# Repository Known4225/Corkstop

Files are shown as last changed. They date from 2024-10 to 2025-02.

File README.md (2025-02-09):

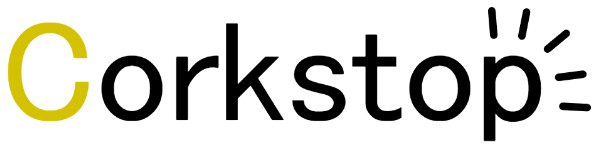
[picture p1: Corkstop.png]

### Remote Ignition System
Corkstop is a single channel ignition system that operates alongside an e-match or igniter to remotely launch a rocket or activate a stationary rocket motor.

## Power:
Corkstop uses a 14v, 24A custom battery to ignite e-matches and igniters.
## Range:
Corkstop uses a 433MHz LoRa radio, meaning it should support ranges up to half a mile or more in optimal conditions.
## How to use:
Connect the battery to the XT60 plug on the receiver box, use the alligator clips from the receiver box to connect an e-match or igniter. The continuity LED on the receiver will indicate whether the match is properly connected. GREEN indicates continuity, while RED indicates that the circuit is broken. There is no power switch on the receiver, it is active at all times if the battery is plugged in.

Continuity information is also available through the continuity LED on the controller. The controller has a power switch. The blue RF light will pulse on and off once a second, if the blue RF light is not pulsing then it means the controller could not connect to the receiver. Verify both RF connectivity and circuit continuity before attempting to ignite.

To ignite the charge, hold down the blue ARM button and verify that the control box is emitting an audible tone. Then, with the ARM button held down, press the red IGNITE button. This will light the e-match or igniter on the receiver side.

## Design Sketch:

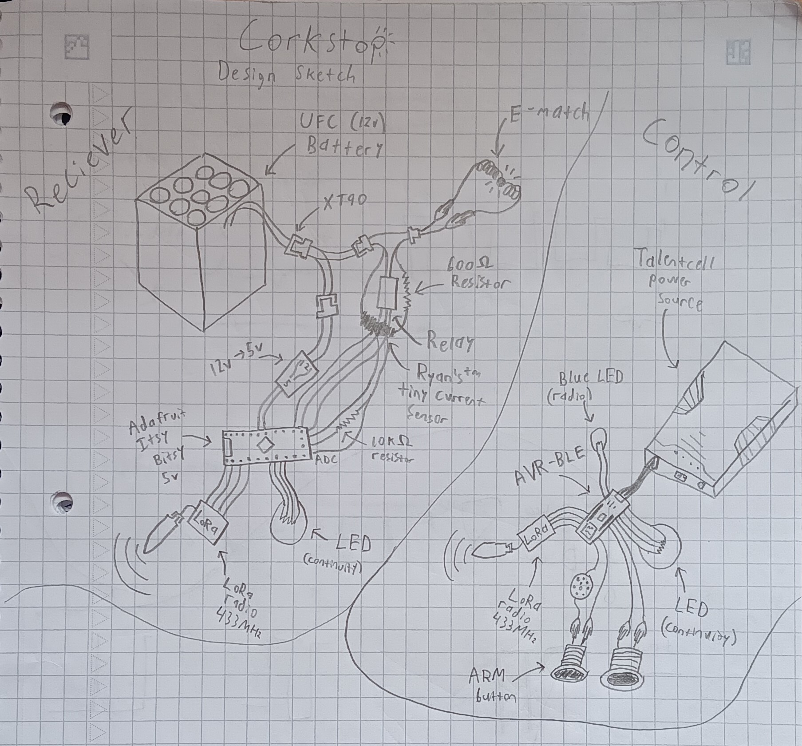
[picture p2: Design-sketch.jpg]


*note that the battery is actually 14v, not 12v. And the resistor value has been updated to 700Ω
*note that the XT60 connector is used, not the XT90

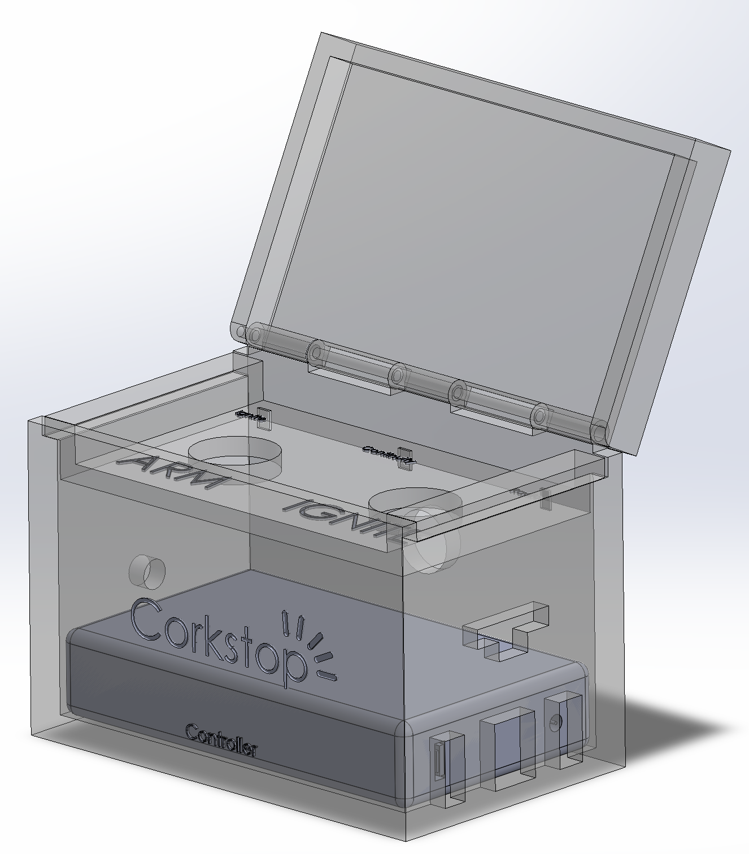
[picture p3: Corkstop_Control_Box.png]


## Product:



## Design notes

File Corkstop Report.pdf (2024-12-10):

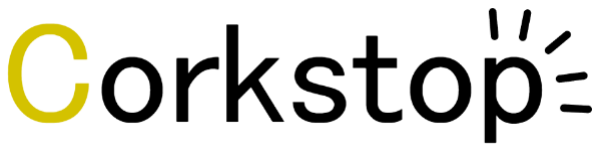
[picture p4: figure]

## Remote Ignition System

Corkstop is a single channel ignition system that operates alongside an e-match or igniter to remotely launch a rocket or activate a stationary rocket motor.

This project was made for use on the UMN rocket team (https://rkt.aem.umn.edu/) as an SRAD (student research and developed) remote ignition system for test rockets, static fires, and launches.

Corkstop consists of a controller box and receiver box, each equipped with a microcontroller, radio, and portable power source.

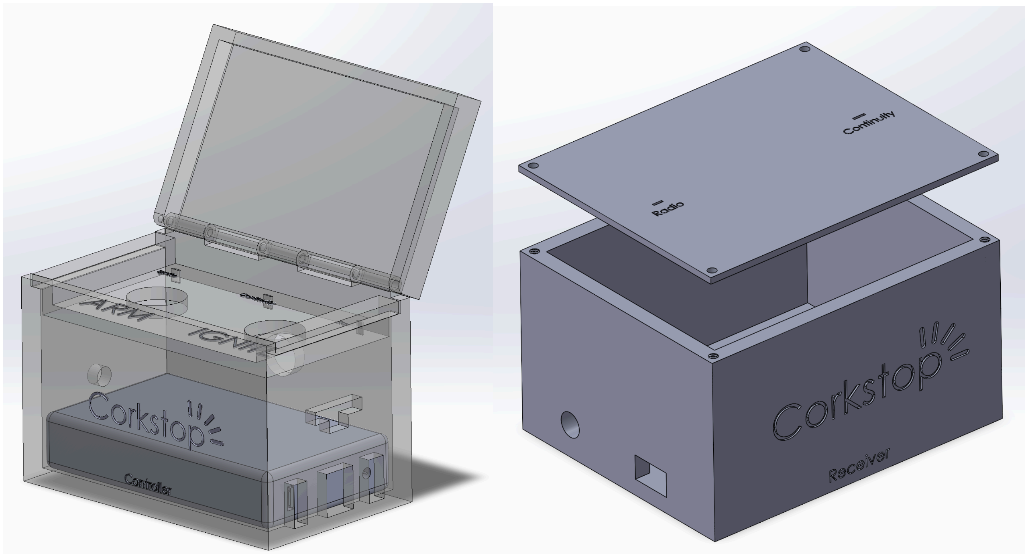
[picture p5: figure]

All the code and CAD can be found here. (https://github.com/Known4225/Corkstop)

# Design and Implementation

Here is the full BOM for this project:
1x Portable power source (https://www.amazon.com/TalentCell-Rechargeable-12000mAh-Multi-led-indicator/dp/B00ME3ZH7C)

1x AVR-BLE board (https://www.microchip.com/en-us/development-tool/dt100111)
1x ItsyBitsy 5v board (https://www.adafruit.com/product/3677)
2x LoRa breakout (https://www.adafruit.com/product/3072)
2x 433MHz antenna (https://www.amazon.com/Antenna-Frequency-Connector-SMA-Male-Receivers/dp/B0C1FCZM94)
1x XT60 Splitter (https://www.amazon.com/RIIEYOCA-Connector-Extension-Quadcopter-XT60-Male/dp/B09L62W679)
2x XT60 connector (https://www.amazon.com/Upgrade-Extension-Connector-Adapter-Silicone/dp/B0B4H5CCR3)
1x DC Buzzer (https://www.amazon.com/Electronic-Continuous-Computers-Automotive-Equipment/dp/B08KW6HB1P)
1x DC-DC converter (https://www.amazon.com/Converter-Voltage-Waterproof-Regulator-Step-Down/dp/B07Y2V1F8V)
1x 5v Relay (https://www.amazon.com/Tolako-Arduino-Indicator-Channel-Official/dp/B00VRUAHLE)
1x 700Ω resistor (https://www.digikey.com/en/products/detail/vishay-dale/CW02B700R0JE70/1169042)
2x Arcade button (https://www.amazon.com/EG-STARTS-Illuminated-Buttons-Raspberry/dp/B01N11BDX9)
2x Alligator Clips
1x Photoresistor
1x Blue LED
2x Cyan LED
3x Multicolour LED
1x 10kΩ resistor
∞x E-matches
1x UFC battery (12.7v, pictured below)

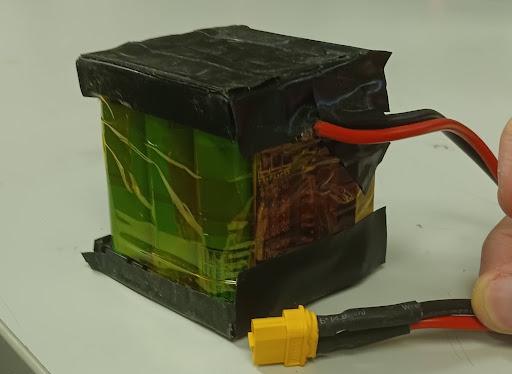
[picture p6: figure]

## Circuit:

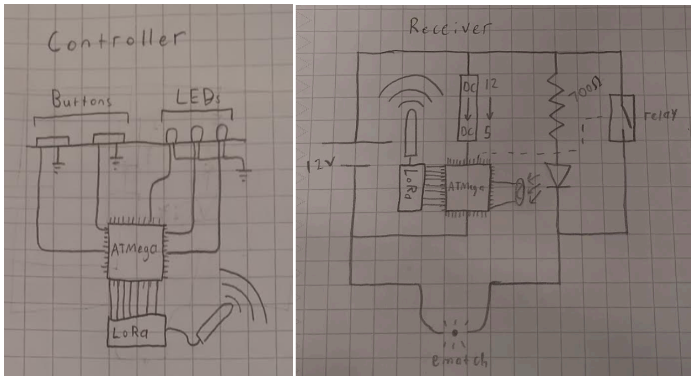
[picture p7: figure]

The basic idea is that a large amount of current (> 300mA) will cause the ematch to ignite. That current is supplied by the UFC battery on the receiver’s end. When the relay is triggered, the battery is shorted, causing a large amount of current to flow through the ematch. While the relay is not triggered, there is a small amount of current (about 15 milliamps) flowing through the ematch. This current is not enough to blow the ematch, but it is enough to light an LED (pictured directly below the 700Ω resistor). The light from the LED is detected by a photoresistor, and the information is recorded by the ATMega on the receiver.

If the ematch is connected improperly, or not connected at all, then the LED is not glowing, as the circuit is not complete. This is called continuity. When the circuit is closed it is said to “have continuity”, when it is open it “does not have continuity”. Both the receiver and controller boxes have a continuity status light, which is green to indicate continuity, and red to indicate loss of continuity. The receiver box uses the photoresistor along with its ADC to gather this continuity information. It then sends that information to the controller box over the LoRa radio.

## Radio:

Both boxes use an SX1276 (https://cdn-shop.adafruit.com/product-files/3179/sx1276_77_78_79.pdf) LoRa radio module. These radios interface over SPI and make use of an interrupt pin for incoming messages. The Corkstop™ custom radio protocol works via request response. The controller box, if on, periodically sends the ASCII string “cork” once a second. The receiver box responds to this by sending either “stop” or “stal”. “stop” indicates that it has continuity on the circuit, and “stal” indicates no continuity. When either radio receives a message, it will turn their cyan radio LED on with a timer to expire the LED in half a second. This means that the cyan radio LED should be blinking every half second if both radios are connected. If either radio disconnects both radio lights remain off.

When the controller wants to send the ignition message, it sends the ASCII string “IGNITE”. The receiver will, after verifying continuity, trigger the relay to short the circuit. If continuity is not met when the ignition signal is received, the receiver will not trigger the relay and will send back “cant” in response. Otherwise, the relay will be triggered for 0.1 seconds and the receiver will send back “done” in response. The closing of the relay should ignite the ematch.

No CRC or checksums are used in the Corkstop™ custom radio protocol. Any malicious actor could send the ASCII strings over 433MHz frequency to attempt to trigger ignition. This also means that multiple Corkstop™ controller -> receiver pairs are not currently possible.

Additionally, libraries RadioHead (https://github.com/PaulStoffregen/RadioHead) and AVR_LoRa (https://github.com/kpierzynski/AVR_LoRa) were used in this project. Thanks to Paul Stoffregen, (http://paulstoffregen) Kurt E, (https://github.com/KurtE) and kpierzynski. (https://github.com/kpierzynski)

## Challenges:

This device is relatively simple, the main challenge was limited time. The initial design concept was created a month before the final product was complete, which is impressive if not a little irresponsible for a device that has a number of safety considerations.

The only design difficulty was figuring out how to integrate the continuity sensor. Current sensors exist, but most of them are not built for these small amounts of currents (10s of milliamps). The LED taped to a photoresistor is certainly unique, but non-standard and potentially dangerous. If the LED burns out then the device will report no continuity even when there is (which is the most dangerous case). I tested the merits of the idea with an arduino and a breadboard three weeks before the project was due, and it seemed like it worked (in ideal environmental conditions that is). Certainly some more thought should have been put into it.

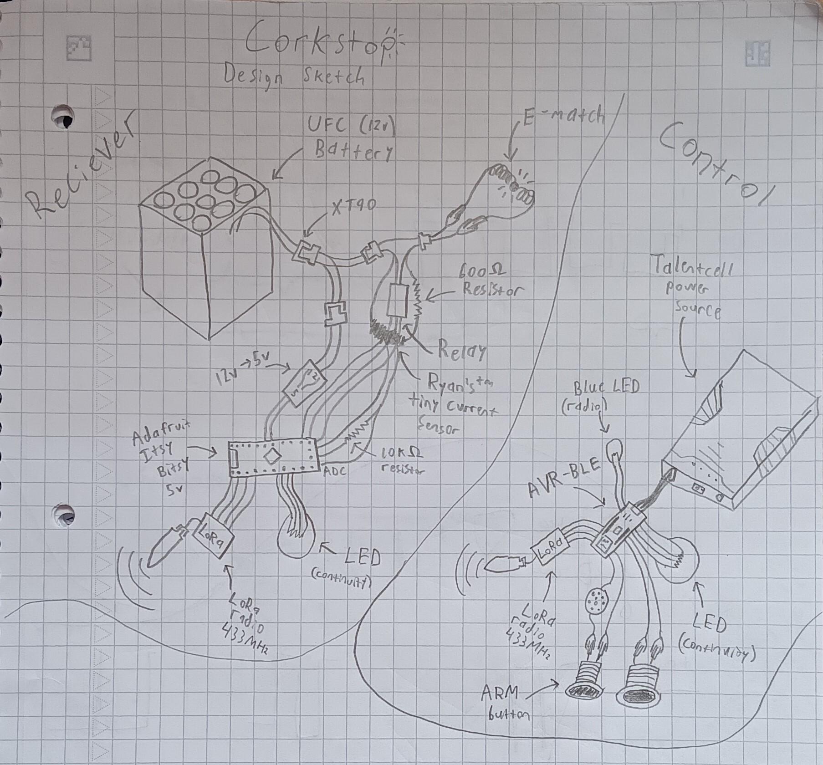
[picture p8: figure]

There were considerable manufacturing challenges, mostly due to a fairly large number of custom parts. I soldered XT60 connectors to the DC -> DC converter, as well as the resistor, current sensing LED, and alligator clips (with the heads cut off). The relay required custom wire with a molex crimp head, and that wire also had to be soldered in with the rest. I put some sleeves over the wire and heat shrunk them together, but this process was fairly difficult, especially at a three-way junction of relay, alligator clip, and LED which I had to redo twice (once when I put the LED on backwards, and again when the LED burned out under mysterious circumstances). I also needed more pins than the AVR-BLE could provide, so I ended up hijacking a few of the BLE pins (UART tx to BLE, as well as reset pin) by soldering wires onto the pads directly. That process was harder than I anticipated (and I totally destroyed the BLE in the process).

The other manufacturing challenge was CAD and 3D printing. Initial designs were finished in CAD about a week before the project was due, and I spent most of thanksgiving break printing them. Only one failed print, but some overlooked design quirks (buzzer hole was not big enough, screw taps did not work, caliper revealed that many of my holes were too small, luckily was caught before printing).

Finally, the assembly process was not difficult but was frustrating. I ended up stuffing all the wires in the box and hoping none of them disconnected. I also decided later to solder an extra antenna to the radio modules to increase range. This was very difficult to do after assembly had been completed.

# Final Product

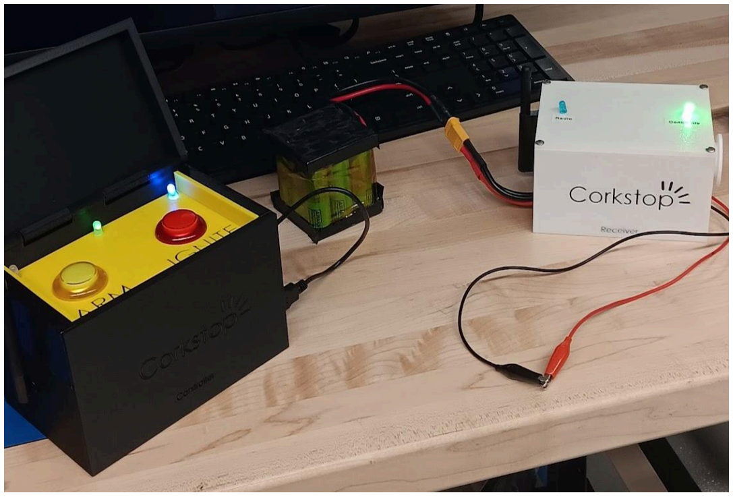
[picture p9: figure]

In total, despite the rushed process, the device was working with all of its features on demo day. There were two tests prior to the due date, one with the electronics pre-assembly and another after the project had been initially completed. Both tests successfully ignited the ematch and every feature worked. Two more ematches were ignited on demo day. The current product has a 100% success rate so far.

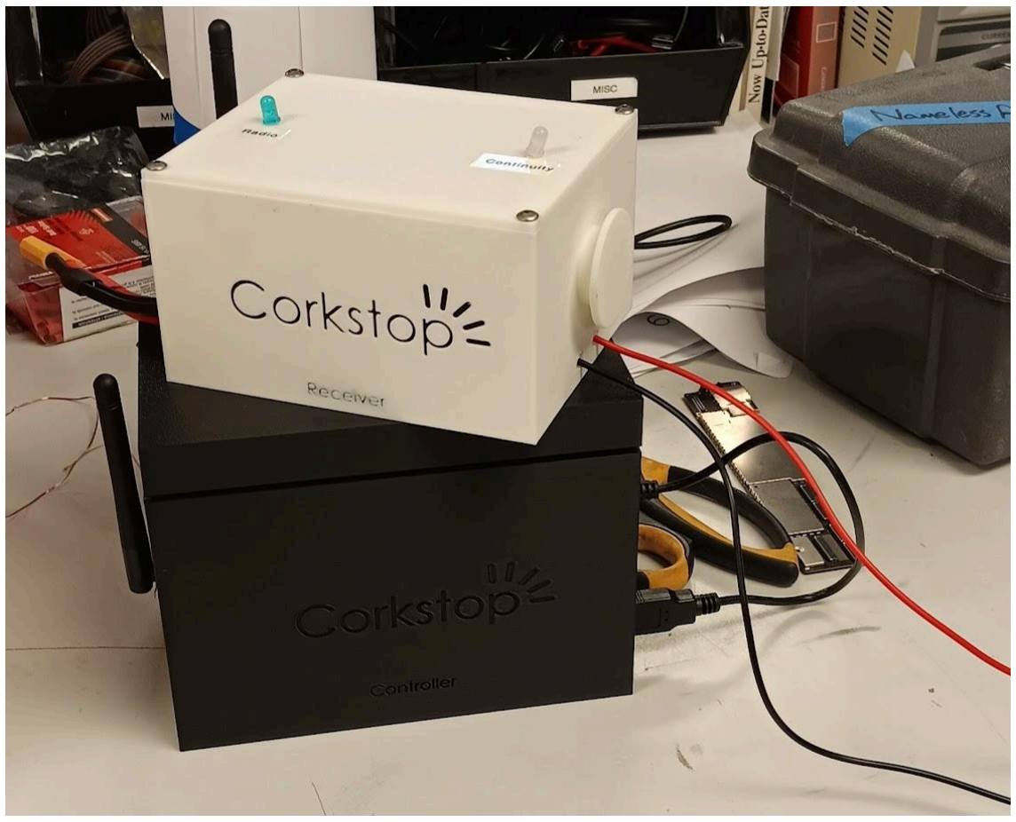
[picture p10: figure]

Every initial project goal was hit except for the range. The last range test gave poor results (~100ft), but I have added an extra antenna since then.

Overall, I am not totally satisfied by the quality and fragility of the project. I would’ve preferred it to be a lot more robust, and with more consideration for safety.

# Reflection

There are two main improvements that I would like to make to this device.

The first is radio and range. Upon testing the range of the device, it was only able to operate at around 100ft, which is not as far as the LoRa modules should be capable of. With more time and more knowledge of RF and antennas this could be improved.

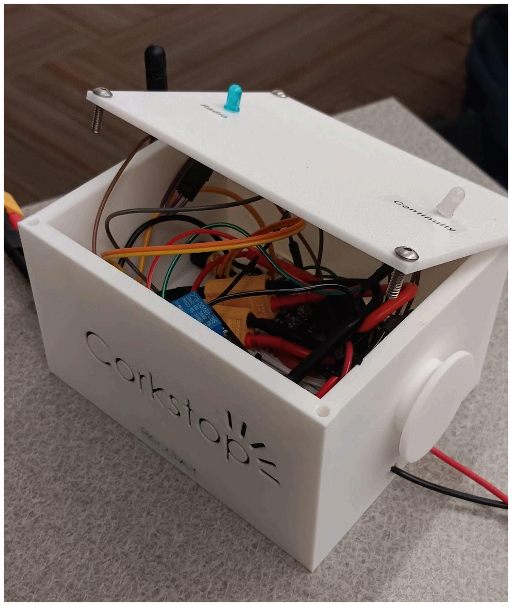
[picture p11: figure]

The second is internal wiring. It is a mess inside the boxes and it is very likely that a wire can come unplugged just by shaking the devices minimally. Ideally a whole PCB could be designed, but a solder-in breadboard would also probably suffice, along with better cable management. These boxes also probably would not fair well in unideal weather conditions. The tape on the LEDs would fail in the New Mexico Deserts, none of the boxes are waterproof, and the radios need direct line of sight.

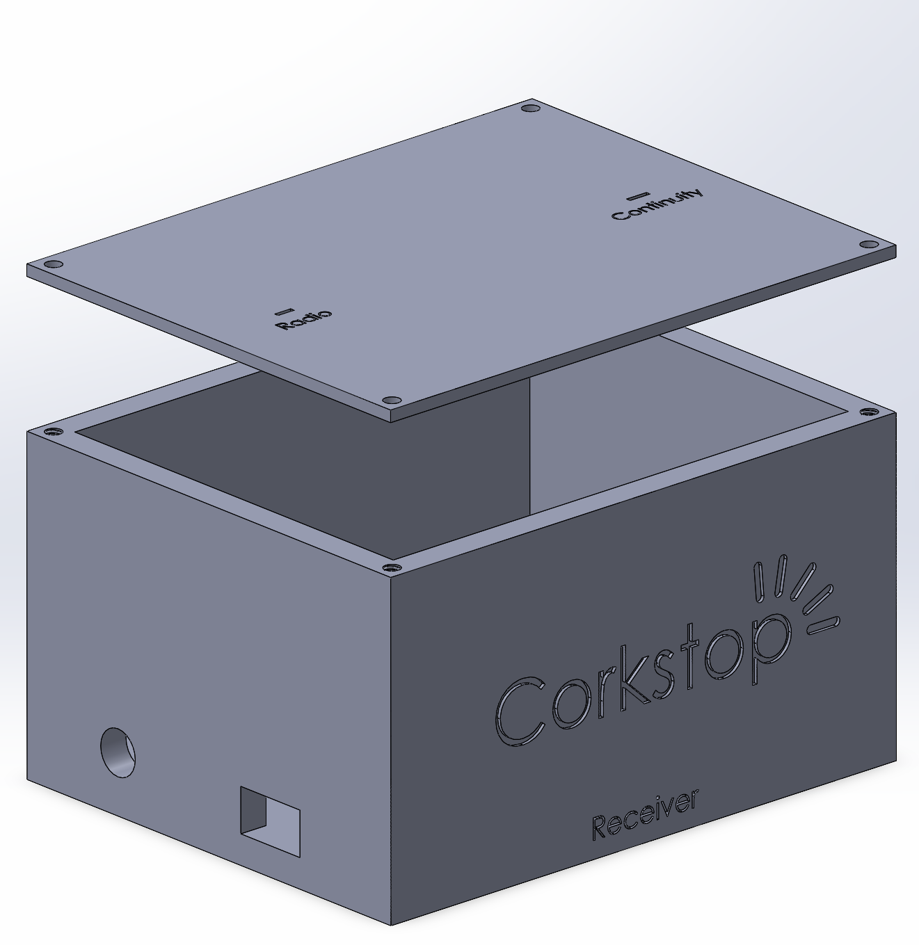
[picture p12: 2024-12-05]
Corkstop_Receive_Box.png

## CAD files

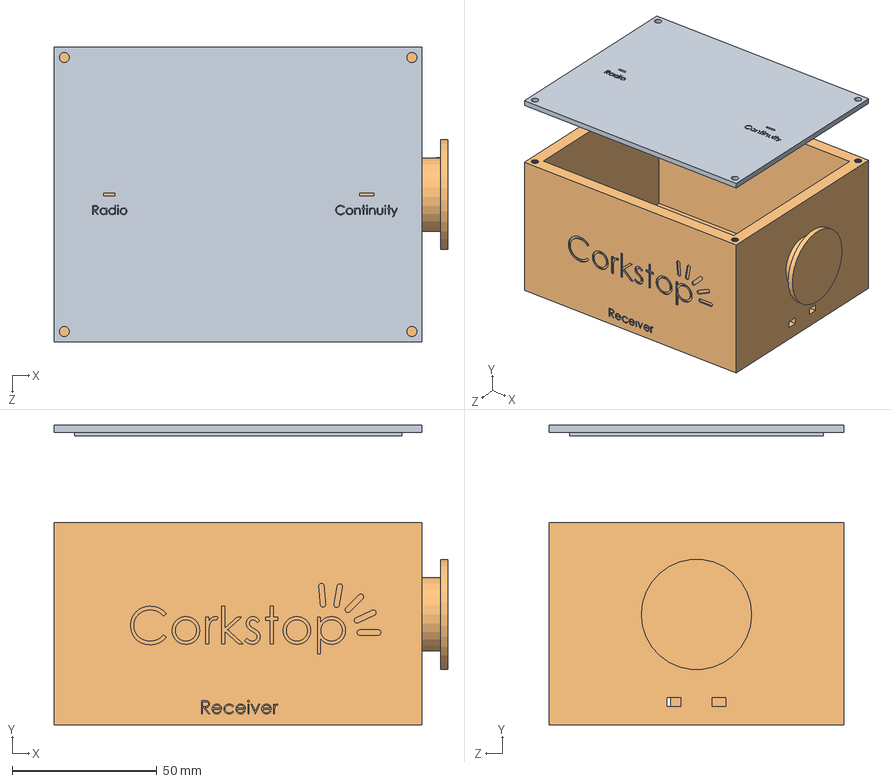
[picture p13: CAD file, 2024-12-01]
Receive.SLDASM
135.9 x 103.4 x 101.6 mm
ReceiveCase
RecieveLid

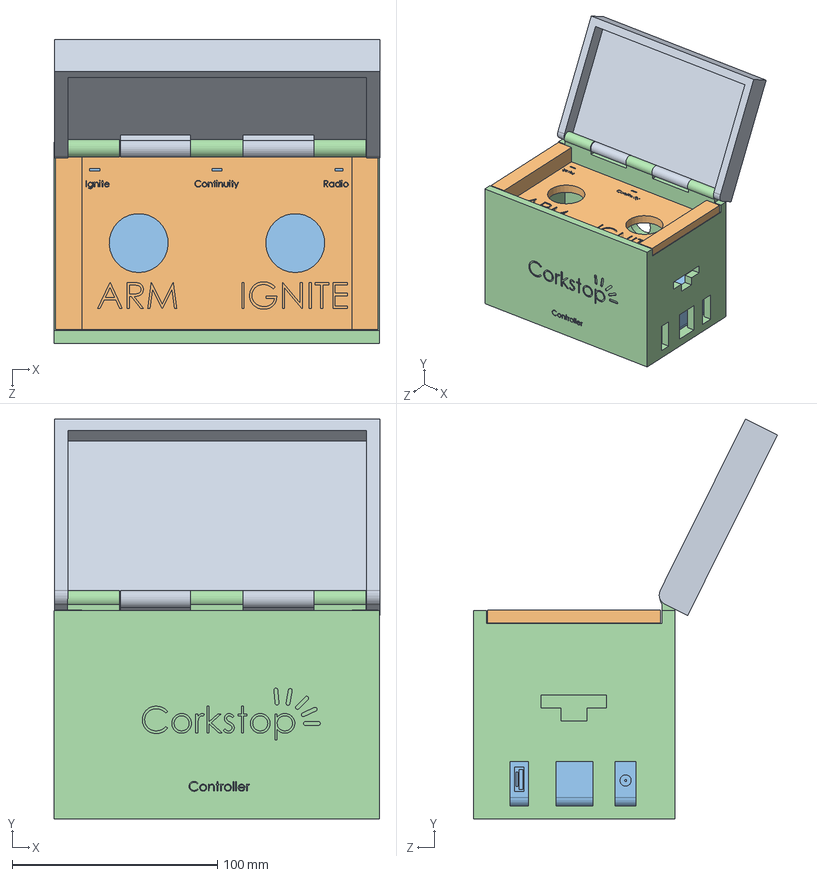
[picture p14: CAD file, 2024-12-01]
Control.SLDASM
158.5 x 194.7 x 148.0 mm
ControlCase
TalentcellPower
ControlTopShelf
ControlLid

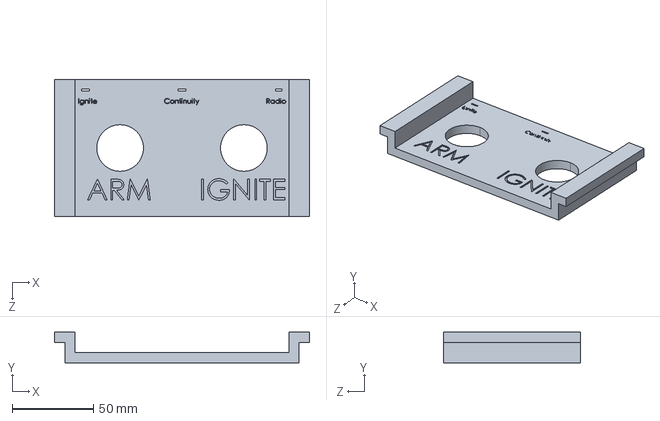
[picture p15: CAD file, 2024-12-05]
ControlBox/ControlTopShelf.STEP
157.0 x 19.0 x 84.1 mm

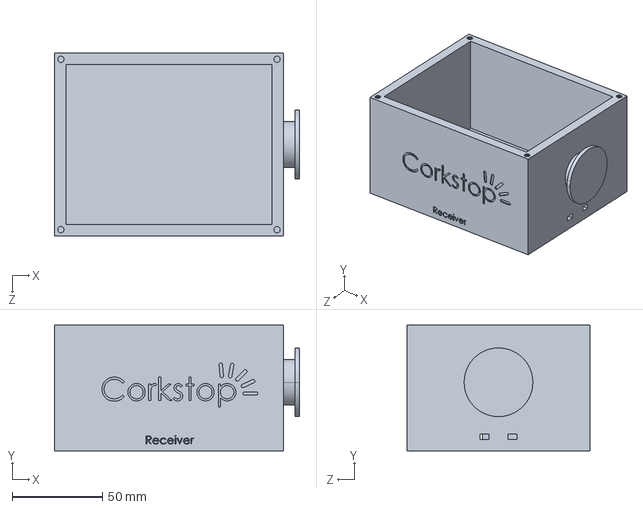
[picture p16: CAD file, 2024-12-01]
ReceiveBox/ReceiveCase.STEP
135.9 x 69.8 x 101.6 mm

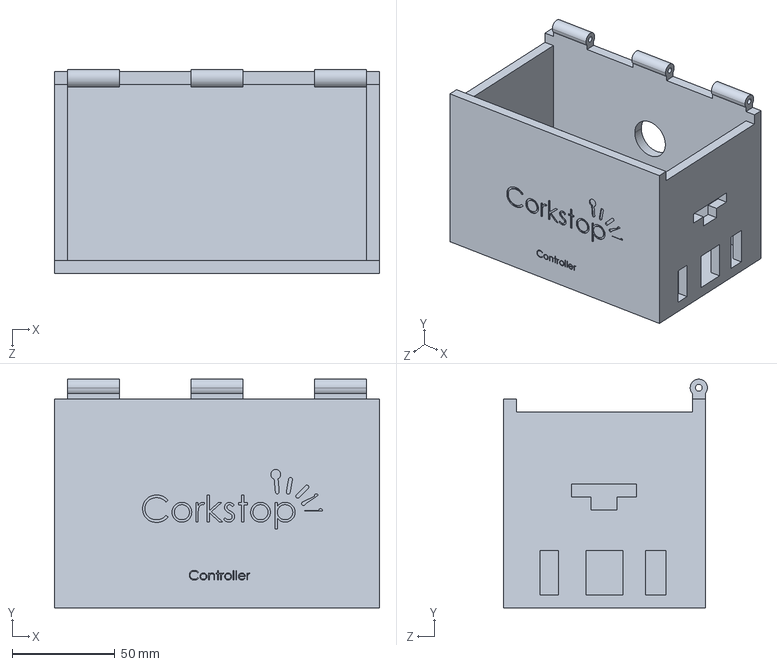
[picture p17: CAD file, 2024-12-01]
ControlBox/ControlCase.STEP
158.2 x 111.3 x 99.2 mm

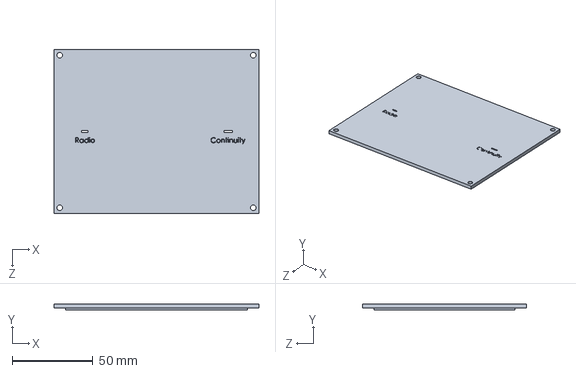
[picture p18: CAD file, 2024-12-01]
ReceiveBox/RecieveLid.STEP
127.0 x 3.81 x 101.6 mm

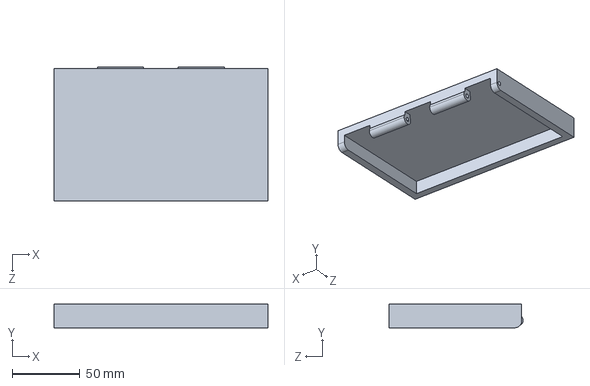
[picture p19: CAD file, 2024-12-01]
ControlBox/ControlLid.STEP
158.2 x 17.4 x 99.2 mm

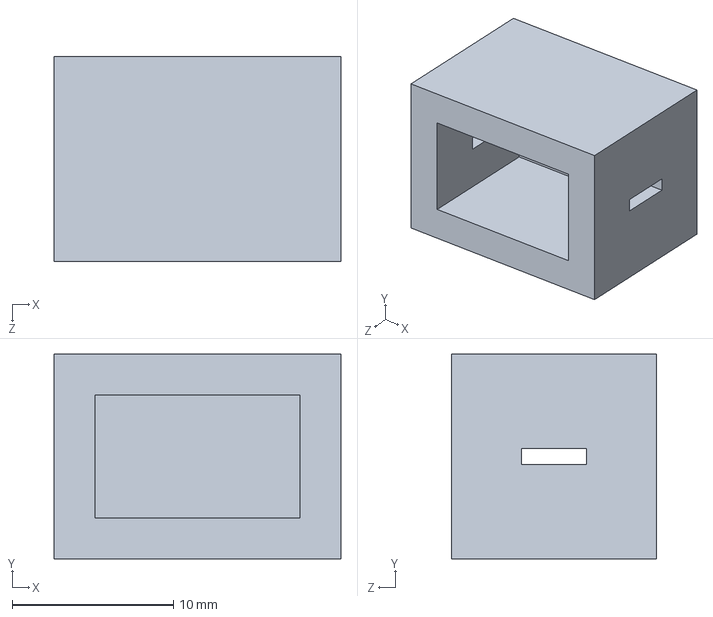
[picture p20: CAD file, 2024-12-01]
CurrentSensor.SLDPRT
17.8 x 12.7 x 12.7 mm

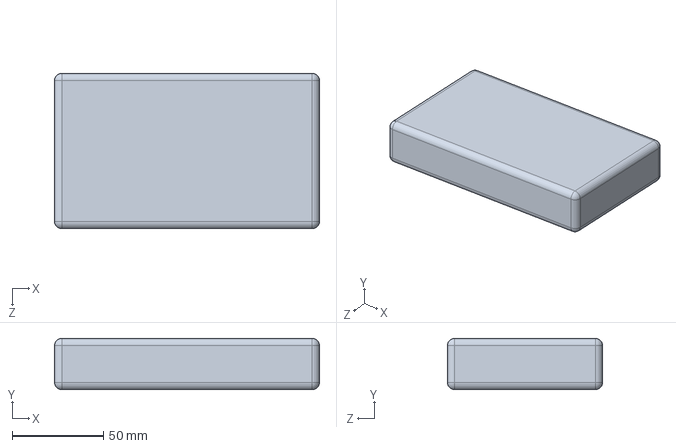
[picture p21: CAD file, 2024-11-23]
TalentcellPower.SLDPRT
145.0 x 28.0 x 85.0 mm

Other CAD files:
ControlTopShelf.SLDPRT
RecieveLid.SLDPRT
ReceiveBox/CurrentSensor.STEP
ControlLid.SLDPRT
ControlCase.SLDPRT
ReceiveCase.SLDPRT

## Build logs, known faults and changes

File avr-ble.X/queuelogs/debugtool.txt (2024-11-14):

3430 1731542538655 GEN4_TO_CONTROLLER_LOG:GEN4_CONNECT_INT_LOG Post:SetLEDBrightness
3430 1731542538655 GEN4_TO_CONTROLLER_LOG:GEN4_CONNECT_INT_LOG Return Value
3430 1731542538655 GEN4_TO_CONTROLLER_LOG:GEN4_CONNECT_INT_LOG none
3430 1731542538655 GEN4_TO_CONTROLLER_LOG:GEN4_CONNECT_INT_LOG Return End

3430 1731542538655 GEN4_TO_CONTROLLER_LOG:GEN4_CONNECT_INT_LOG Pre:SetToolInfo
3430 1731542538655 GEN4_TO_CONTROLLER_LOG:GEN4_CONNECT_INT_LOG Payload
3430 1731542538655 GEN4_TO_CONTROLLER_LOG:GEN4_CONNECT_INT_LOG ToolInfo: Values:
3430 1731542538655 GEN4_TO_CONTROLLER_LOG:GEN4_CONNECT_INT_LOG ToolInfo: speedLevel = 1, PGCResistance = 4700, PGDResistance = 4700, PGCPullDir = PullDown, PGDPullDir = PullDown, ICSPSelected = Wire2
3430 1731542538655 GEN4_TO_CONTROLLER_LOG:GEN4_CONNECT_INT_LOG Payload End
3430 1731542538655 GEN4_TO_CONTROLLER_LOG:GEN4_CONNECT_INT_LOG Post:SetToolInfo
3430 1731542538655 GEN4_TO_CONTROLLER_LOG:GEN4_CONNECT_INT_LOG Return Value
3430 1731542538655 GEN4_TO_CONTROLLER_LOG:GEN4_CONNECT_INT_LOG none
3430 1731542538655 GEN4_TO_CONTROLLER_LOG:GEN4_CONNECT_INT_LOG Return End

3430 1731542538656 GEN4_TO_CONTROLLER_LOG:GEN4_CONNECT_INT_LOG Pre:GetTargetIDInfo
3430 1731542538656 GEN4_TO_CONTROLLER_LOG:GEN4_CONNECT_INT_LOG Payload
3430 1731542538656 GEN4_TO_CONTROLLER_LOG:GEN4_CONNECT_INT_LOG null
3430 1731542538656 GEN4_TO_CONTROLLER_LOG:GEN4_CONNECT_INT_LOG Payload End
3430 1731542538656 NativeController::GetTargetIDInfo entry
3430 1731542538656 pro JtagIce3 [0x12] <<< 01 00 01 31 02 F4 01 
3430 1731542538660 pro JtagIce3 [0x12] >>> 80 00 
3430 1731542538660 pro JtagIce3 [0x12] <<< 01 00 00 00 01 05 
3430 1731542538664 pro JtagIce3 [0x12] >>> 80 00 
3430 1731542538664 pro JtagIce3 [0x12] <<< 01 00 00 01 01 01 
3430 1731542538668 pro JtagIce3 [0x12] >>> 80 00 
3430 1731542538668 pro JtagIce3 [0x12] <<< 01 00 01 00 01 08 
3430 1731542538672 pro JtagIce3 [0x12] >>> 80 00 
3430 1731542538672 pro JtagIce3 [0x12] <<< 01 00 02 00 30 00 40 80 40 00 10 80 0F 94 11 8C 0A 98 08 DC 05 DC 05 00 80 00 00 00 01 40 00 0A 05 FF 00 FF 00 00 14 00 13 00 11 80 12 8A 12 30 95 00 00 00 01 
3430 1731542538676 pro JtagIce3 [0x12] >>> 80 00 
3430 1731542538676 pro JtagIce3 [0x12] <<< 01 00 03 06 01 00 
3430 1731542538680 pro JtagIce3 [0x12] >>> 80 00 
3430 1731542538680 pro JtagIce3 [0x12] <<< 10 00 00 
3430 1731542538701 pro JtagIce3 [0x12] >>> 84 00 6D 65 67 61 00 
3430 1731542538701 pro JtagIce3 [0x12] <<< 01 00 03 06 01 00 
3430 1731542538705 pro JtagIce3 [0x12] >>> 80 00 
3430 1731542538705 pro JtagIce3 [0x12] <<< 15 00 
3430 1731542538772 pro JtagIce3 [0x12] >>> 80 00 
3430 1731542538772 pro JtagIce3 [0x12] <<< 21 00 B4 00 11 00 00 03 00 00 00 
3430 1731542538776 pro JtagIce3 [0x12] >>> 84 00 1E 95 30 00 
3430 1731542538776 pro JtagIce3 [0x12] <<< 21 00 B4 00 11 00 00 03 00 00 00 
3430 1731542538780 pro JtagIce3 [0x12] >>> 84 00 1E 95 30 00 
3430 1731542538780 pro JtagIce3 [0x12] <<< 21 00 B4 00 11 00 00 03 00 00 00 
3430 1731542538784 pro JtagIce3 [0x12] >>> 84 00 1E 95 30 00 
3430 1731542538784 pro JtagIce3 [0x12] <<< 21 00 B2 01 0F 00 00 01 00 00 00 
3430 1731542538788 pro JtagIce3 [0x12] >>> 84 00 01 00 
3430 1731542538788 pro JtagIce3 [0x12] <<< 16 00 
3430 1731542538792 pro JtagIce3 [0x12] >>> 80 00 
3430 1731542538792 pro JtagIce3 [0x12] <<< 11 00 
3430 1731542538796 pro JtagIce3 [0x12] >>> 80 00 
3430 1731542538796 pro JtagIce3 [0x01] <<< 11 00 00 
3430 1731542538800 pro JtagIce3 [0x01] >>> 80 00 
3430 1731542538800 NativeController::GetTargetIDInfo exit device ID 0x1e9530
3430 1731542538800 GEN4_TO_CONTROLLER_LOG:GEN4_CONNECT_INT_LOG Post:GetTargetIDInfo
3430 1731542538800 GEN4_TO_CONTROLLER_LOG:GEN4_CONNECT_INT_LOG Return Value
3430 1731542538800 GEN4_TO_CONTROLLER_LOG:GEN4_CONNECT_INT_LOG TargetIDInfo: Values:
3430 1731542538800 GEN4_TO_CONTROLLER_LOG:GEN4_CONNECT_INT_LOG TargetIDInfo: DeviceID = 001e9530
3430 1731542538800 GEN4_TO_CONTROLLER_LOG:GEN4_CONNECT_INT_LOG Return End

3430 1731542538804 GEN4_TO_CONTROLLER_LOG:GEN4_PROGRAM_INT_LOG_ATmega3208 Pre:SendOperation
3430 1731542538804 GEN4_TO_CONTROLLER_LOG:GEN4_PROGRAM_INT_LOG_ATmega3208 Payload
3430 1731542538804 GEN4_TO_CONTROLLER_LOG:GEN4_PROGRAM_INT_LOG_ATmega3208 OperationInfo: Values:
3430 1731542538804 GEN4_TO_CONTROLLER_LOG:GEN4_PROGRAM_INT_LOG_ATmega3208 OperationInfo: Type = erase, Mask = 00000000, Erase = false, Production Mode = true
3430 1731542538804 GEN4_TO_CONTROLLER_LOG:GEN4_PROGRAM_INT_LOG_ATmega3208 TransferInfo: Start = 0, End = 7fff, Buffer Length = 0, Type = Pgm, Mask = 00000000
3430 1731542538804 GEN4_TO_CONTROLLER_LOG:GEN4_PROGRAM_INT_LOG_ATmega3208 TransferInfo: Start = 1280, End = 1288, Buffer Length = 0, Type = Cfg, Mask = 00000000
3430 1731542538804 GEN4_TO_CONTROLLER_LOG:GEN4_PROGRAM_INT_LOG_ATmega3208 TransferInfo: Start = 128a, End = 128a, Buffer Length = 0, Type = Cfg, Mask = 00000000
3430 1731542538804 GEN4_TO_CONTROLLER_LOG:GEN4_PROGRAM_INT_LOG_ATmega3208 TransferInfo: Start = 1400, End = 14ff, Buffer Length = 0, Type = EEData, Mask = 00000000
3430 1731542538804 GEN4_TO_CONTROLLER_LOG:GEN4_PROGRAM_INT_LOG_ATmega3208 TransferInfo: Start = 1300, End = 133f, Buffer Length = 0, Type = UserID, Mask = 00000000
3430 1731542538804 GEN4_TO_CONTROLLER_LOG:GEN4_PROGRAM_INT_LOG_ATmega3208 Payload End
3430 1731542538804 pro JtagIce3 [0x12] <<< 01 00 01 31 02 F4 01 
3430 1731542538807 pro JtagIce3 [0x12] >>> 80 00 
3430 1731542538807 pro JtagIce3 [0x12] <<< 01 00 00 00 01 05 
3430 1731542538811 pro JtagIce3 [0x12] >>> 80 00 
3430 1731542538811 pro JtagIce3 [0x12] <<< 01 00 00 01 01 01 
3430 1731542538815 pro JtagIce3 [0x12] >>> 80 00 
3430 1731542538815 pro JtagIce3 [0x12] <<< 01 00 01 00 01 08 
3430 1731542538819 pro JtagIce3 [0x12] >>> 80 00 
3430 1731542538819 pro JtagIce3 [0x12] <<< 01 00 02 00 30 00 40 80 40 00 10 80 0F 94 11 8C 0A 98 08 DC 05 DC 05 00 80 00 00 00 01 40 00 0A 05 FF 00 FF 00 00 14 00 13 00 11 80 12 8A 12 30 95 00 00 00 01 
3430 1731542538823 pro JtagIce3 [0x12] >>> 80 00 
3430 1731542538823 pro JtagIce3 [0x12] <<< 01 00 03 06 01 00 
3430 1731542538827 pro JtagIce3 [0x12] >>> 80 00 
3430 1731542538827 pro JtagIce3 [0x12] <<< 10 00 00 
3430 1731542538848 pro JtagIce3 [0x12] >>> 84 00 6D 65 67 61 00 
3430 1731542538848 pro JtagIce3 [0x12] <<< 01 00 03 06 01 00 
3430 1731542538852 pro JtagIce3 [0x12] >>> 80 00 
3430 1731542538852 pro JtagIce3 [0x12] <<< 15 00 
3430 1731542538919 pro JtagIce3 [0x12] >>> 80 00 
3430 1731542538919 pro JtagIce3 [0x12] <<< 21 00 B4 00 11 00 00 03 00 00 00 
3430 1731542538923 pro JtagIce3 [0x12] >>> 84 00 1E 95 30 00 
3430 1731542538923 pro JtagIce3 [0x12] <<< 20 00 00 00 00 00 00 
3430 1731542538930 pro JtagIce3 [0x12] >>> 80 00 
3430 1731542538930 pro JtagIce3 [0x12] <<< 21 00 B2 85 12 00 00 01 00 00 00 
3430 1731542538934 pro JtagIce3 [0x12] >>> 84 00 C0 00 
3430 1731542538934 pro JtagIce3 [0x12] <<< 23 00 B2 85 12 00 00 01 00 00 00 00 C0 
3430 1731542538942 pro JtagIce3 [0x12] >>> 80 00 
3430 1731542538942 pro JtagIce3 [0x12] <<< 21 00 B2 85 12 00 00 01 00 00 00 
3430 1731542538946 pro JtagIce3 [0x12] >>> 84 00 C0 00 
3430 1731542538946 pro JtagIce3 [0x12] <<< 23 00 B2 85 12 00 00 01 00 00 00 00 C0 
3430 1731542538954 pro JtagIce3 [0x12] >>> 80 00 
3430 1731542538954 pro JtagIce3 [0x12] <<< 20 00 00 00 00 00 00 
3430 1731542538961 pro JtagIce3 [0x12] >>> 80 00 
3430 1731542538961 GEN4_TO_CONTROLLER_LOG:GEN4_PROGRAM_INT_LOG_ATmega3208 Post:SendOperation
3430 1731542538961 GEN4_TO_CONTROLLER_LOG:GEN4_PROGRAM_INT_LOG_ATmega3208 Return Value
3430 1731542538961 GEN4_TO_CONTROLLER_LOG:GEN4_PROGRAM_INT_LOG_ATmega3208 None
3430 1731542538961 GEN4_TO_CONTROLLER_LOG:GEN4_PROGRAM_INT_LOG_ATmega3208 Return End

3430 1731542538962 GEN4_TO_CONTROLLER_LOG:GEN4_PROGRAM_INT_LOG_ATmega3208 Pre:SendOperation
3430 1731542538962 GEN4_TO_CONTROLLER_LOG:GEN4_PROGRAM_INT_LOG_ATmega3208 Payload
3430 1731542538962 GEN4_TO_CONTROLLER_LOG:GEN4_PROGRAM_INT_LOG_ATmega3208 OperationInfo: Values:
3430 1731542538962 GEN4_TO_CONTROLLER_LOG:GEN4_PROGRAM_INT_LOG_ATmega3208 OperationInfo: Type = write, Mask = 00000000, Erase = false, Production Mode = true
3430 1731542538962 GEN4_TO_CONTROLLER_LOG:GEN4_PROGRAM_INT_LOG_ATmega3208 TransferInfo: Start = 0, End = cff, Buffer Length = 3328, Type = Pgm, Mask = 00000000
3430 1731542538962 GEN4_TO_CONTROLLER_LOG:GEN4_PROGRAM_INT_LOG_ATmega3208 Payload End
3430 1731542538962 pro JtagIce3 [0x12] <<< 23 00 C0 00 00 00 00 80 00 00 00 00 0C 94 4B 00 0C 94 5E 06 0C 94 5E 06 0C 94 5E 06 0C 94 5E 06 0C 94 5E 06 0C 94 E2 05 0C 94 5E 06 0C 94 5E 06 0C 94 5E 06 0C 94 5E 06 0C 94 5E 06 0C 94 5E 06 0C 94 5E 06 0C 94 5E 06 0C 94 5E 06 0C 94 5E 06 0C 94 5E 06 0C 94 5E 06 0C 94 5E 06 0C 94 5E 06 0C 94 5E 06 0C 94 5E 06 0C 94 5E 06 0C 94 5E 06 0C 94 5E 06 0C 94 5E 06 0C 94 5E 06 0C 94 5E 06 0C 94 5E 06 0C 94 5E 06 0C 94 5E 06 
3430 1731542538980 pro JtagIce3 [0x12] >>> 80 00 
3430 1731542538980 pro JtagIce3 [0x12] <<< 23 00 C0 80 00 00 00 80 00 00 00 00 0C 94 5E 06 0C 94 5E 06 0C 94 5E 06 0C 94 5E 06 30 00 31 02 80 00 11 24 1F BE CF EF CD BF DF E3 DE BF E0 E9 F0 E0 40 E0 17 C0 B5 91 A5 91 35 91 25 91 05 91 07 FD 0C C0 95 91 85 91 EF 01 F9 2F E8 2F 05 90 0D 92 A2 17 B3 07 D9 F7 FE 01 04 C0 1D 92 A2 17 B3 07 E1 F7 E5 39 F4 07 31 F7 0E 94 A5 04 0C 94 EF 05 F8 94 FF CF CF 93 DF 93 00 D0 CD B7 DE B7 0E 94 23 05 E0 E0 F4 E0 81 81 84 60 
3430 1731542538998 pro JtagIce3 [0x12] >>> 80 00 
3430 1731542538998 pro JtagIce3 [0x12] <<< 23 00 C0 00 01 00 00 80 00 00 00 00 81 83 81 81 87 7F 81 83 83 89 82 60 83 8B 84 81 84 60 84 83 82 EC 92 EA 01 97 F1 F7 00 C0 84 81 8B 7F 84 83 81 E4 93 E0 01 97 F1 F7 00 00 84 81 84 60 84 83 8D E8 90 E2 01 97 F1 F7 00 00 0E 94 2E 06 BE 01 6F 5F 7F 4F 82 E4 0E 94 0C 05 89 81 82 31 09 F0 40 C0 0E 94 3A 06 60 E8 81 E0 0E 94 51 05 60 E4 7E E0 8F EC 99 E1 0E 94 8A 02 60 E0 8E E0 0E 94 51 05 60 E0 8F E0 0E 94 51 05 BE 01 
3430 1731542539016 pro JtagIce3 [0x12] >>> 80 00 
3430 1731542539016 pro JtagIce3 [0x12] <<< 23 00 C0 80 01 00 00 80 00 00 00 00 6E 5F 7F 4F 8C E0 0E 94 0C 05 6A 81 63 60 8C E0 0E 94 51 05 64 E0 86 E2 0E 94 51 05 60 E0 80 E4 0E 94 51 05 87 E0 0E 94 52 04 87 E0 0E 94 6E 04 81 E0 0E 94 8A 04 84 E1 0E 94 CB 03 0E 94 66 05 0E 94 3F 06 82 EC 92 EA 01 97 F1 F7 00 C0 0E 94 49 06 80 E0 01 C0 81 E0 0F 90 0F 90 DF 91 CF 91 08 95 10 C0 0E 94 1A 06 58 F0 0E 94 13 06 40 F0 29 F4 5F 3F 29 F0 0C 94 34 06 51 11 0C 94 22 06 
3430 1731542539034 pro JtagIce3 [0x12] >>> 80 00 
3430 1731542539035 pro JtagIce3 [0x12] <<< 23 00 C0 00 02 00 00 80 00 00 00 00 0C 94 5B 06 0E 94 12 04 68 F3 99 23 B1 F3 55 23 91 F3 95 1B 55 0B BB 27 AA 27 62 17 73 07 84 07 38 F0 9F 5F 5F 4F 22 0F 33 1F 44 1F AA 1F A9 F3 35 D0 0E 2E 3A F0 E0 E8 32 D0 91 50 50 40 E6 95 00 1C CA F7 2B D0 FE 2F 29 D0 66 0F 77 1F 88 1F BB 1F 26 17 37 07 48 07 AB 07 B0 E8 09 F0 BB 0B 80 2D BF 01 FF 27 93 58 5F 4F 3A F0 9E 3F 51 05 78 F0 0C 94 34 06 0C 94 22 06 5F 3F E4 F3 98 3E 
3430 1731542539052 pro JtagIce3 [0x12] >>> 80 00 
3430 1731542539052 pro JtagIce3 [0x12] <<< 23 00 C0 80 02 00 00 80 00 00 00 00 D4 F3 86 95 77 95 67 95 B7 95 F7 95 9F 5F C9 F7 88 0F 91 1D 96 95 87 95 97 F9 08 95 E1 E0 66 0F 77 1F 88 1F BB 1F 62 17 73 07 84 07 BA 07 20 F0 62 1B 73 0B 84 0B BA 0B EE 1F 88 F7 E0 95 08 95 0F C0 0E 94 13 06 38 F0 0E 94 1A 06 20 F0 95 23 11 F0 0C 94 34 06 0C 94 5B 06 11 24 0C 94 22 06 0E 94 12 04 70 F3 95 9F C1 F3 95 0F 50 E0 55 1F 62 9F F0 01 72 9F BB 27 F0 0D B1 1D 63 9F AA 27 
3430 1731542539070 pro JtagIce3 [0x12] >>> 80 00 
3430 1731542539070 pro JtagIce3 [0x12] <<< 23 00 C0 00 03 00 00 80 00 00 00 00 F0 0D B1 1D AA 1F 64 9F 66 27 B0 0D A1 1D 66 1F 82 9F 22 27 B0 0D A1 1D 62 1F 73 9F B0 0D A1 1D 62 1F 83 9F A0 0D 61 1D 22 1F 74 9F 33 27 A0 0D 61 1D 23 1F 84 9F 60 0D 21 1D 82 2F 76 2F 6A 2F 11 24 9F 57 50 40 9A F0 F1 F0 88 23 4A F0 EE 0F FF 1F BB 1F 66 1F 77 1F 88 1F 91 50 50 40 A9 F7 9E 3F 51 05 80 F0 0C 94 34 06 0C 94 22 06 5F 3F E4 F3 98 3E D4 F3 86 95 77 95 67 95 B7 95 F7 95 
3430 1731542539088 pro JtagIce3 [0x12] >>> 80 00 
3430 1731542539088 pro JtagIce3 [0x12] <<< 23 00 C0 80 03 00 00 80 00 00 00 00 E7 95 9F 5F C1 F7 FE 2B 88 0F 91 1D 96 95 87 95 97 F9 08 95 11 C0 0E 94 13 06 38 F0 0E 94 1A 06 20 F0 39 F4 9F 3F 19 F4 26 F4 0C 94 5B 06 0E F4 E0 95 E7 FB 0C 94 34 06 E9 2F 0E 94 12 04 58 F3 BA 17 62 07 73 07 84 07 95 07 20 F0 79 F4 A6 F5 0C 94 21 06 0E F4 E0 95 0B 2E BA 2F A0 2D 0B 01 B9 01 90 01 0C 01 CA 01 A0 01 11 24 FF 27 59 1B 99 F0 59 3F 50 F4 50 3E 68 F1 1A 16 F0 40 A2 2F 
3430 1731542539106 pro JtagIce3 [0x12] >>> 80 00 
3430 1731542539106 pro JtagIce3 [0x12] <<< 23 00 C0 00 04 00 00 80 00 00 00 00 23 2F 34 2F 44 27 58 5F F3 CF 46 95 37 95 27 95 A7 95 F0 40 53 95 C9 F7 7E F4 1F 16 BA 0B 62 0B 73 0B 84 0B BA F0 91 50 A1 F0 FF 0F BB 1F 66 1F 77 1F 88 1F C2 F7 0E C0 BA 0F 62 1F 73 1F 84 1F 48 F4 87 95 77 95 67 95 B7 95 F7 95 9E 3F 08 F0 B0 CF 93 95 88 0F 08 F0 99 27 EE 0F 97 95 87 95 08 95 1F 93 CF 93 DF 93 00 D0 0F 92 CD B7 DE B7 80 91 01 31 88 23 09 F4 46 C0 BE 01 6E 5F 7F 4F 
3430 1731542539124 pro JtagIce3 [0x12] >>> 80 00 
3430 1731542539124 pro JtagIce3 [0x12] <<< 23 00 C0 80 04 00 00 80 00 00 00 00 82 E1 0E 94 0C 05 6A 81 82 E1 0E 94 51 05 8A 81 85 FF 0C C0 E0 91 FF 30 F0 91 00 31 30 97 89 F1 40 E2 60 E0 80 E0 90 E0 09 95 2B C0 86 FF 29 C0 BE 01 6D 5F 7F 4F 83 E1 0E 94 0C 05 BE 01 6F 5F 7F 4F 80 E1 0E 94 0C 05 69 81 8D E0 0E 94 51 05 6B 81 66 23 61 F0 10 E0 61 2F 70 E0 60 50 70 4D 80 E0 0E 94 0C 05 1F 5F 6B 81 16 17 A8 F3 E0 91 FF 30 F0 91 00 31 30 97 21 F0 40 E4 80 E0 90 E3 
3430 1731542539142 pro JtagIce3 [0x12] >>> 80 00 
3430 1731542539142 pro JtagIce3 [0x12] <<< 23 00 C0 00 05 00 00 80 00 00 00 00 09 95 10 92 01 31 23 96 CD BF DE BF DF 91 CF 91 1F 91 08 95 AF 92 BF 92 CF 92 DF 92 EF 92 FF 92 0F 93 1F 93 CF 93 DF 93 DC 01 CB 01 28 2F 39 2F 4A 2F 5B 2F 60 E0 70 E0 80 E0 90 E0 03 E1 0E 94 F3 04 A1 2C 0F 2E F8 E4 BF 2E F0 2D 0F 2E F8 EE CF 2E F0 2D DD 24 D3 94 E1 2C F1 2C 00 E0 10 E0 0E 94 D6 05 C2 2F B3 2E C4 2E D5 2E E6 2E F7 2E 18 2F D9 2F 00 E1 0E 94 36 04 62 2F 86 E0 0E 94 
3430 1731542539160 pro JtagIce3 [0x12] >>> 80 00 
3430 1731542539160 pro JtagIce3 [0x12] <<< 23 00 C0 80 05 00 00 80 00 00 00 00 51 05 2C 2F 3B 2D 4C 2D 5D 2D 6E 2D 7F 2D 81 2F 9D 2F 08 E0 0E 94 36 04 62 2F 87 E0 0E 94 51 05 6C 2F 88 E0 0E 94 51 05 DF 91 CF 91 1F 91 0F 91 FF 90 EF 90 DF 90 CF 90 BF 90 AF 90 08 95 88 24 99 24 F4 01 E4 01 B0 E4 9F 93 AA 27 9A 15 8B 04 9C 04 ED 05 FE 05 CF 05 D0 07 A1 07 98 F4 AD 2F DC 2F CF 2F FE 2F E9 2D 98 2C 89 2E 98 2F 87 2F 76 2F 65 2F 54 2F 43 2F 32 2F 22 27 B8 50 31 F7 
3430 1731542539178 pro JtagIce3 [0x12] >>> 80 00 
3430 1731542539178 pro JtagIce3 [0x12] <<< 23 00 C0 00 06 00 00 80 00 00 00 00 BF 91 27 C0 1B 2E BF 91 BB 27 22 0F 33 1F 44 1F 55 1F 66 1F 77 1F 88 1F 99 1F 88 1C 99 1C EE 1F FF 1F CC 1F DD 1F AA 1F BB 1F 8A 14 9B 04 EC 05 FD 05 CE 05 DF 05 A0 07 B1 07 48 F0 8A 18 9B 08 EC 09 FD 09 CE 09 DF 09 A0 0B B1 0B 21 60 1A 94 E1 F6 2E F4 94 01 AF 01 BE 01 CD 01 00 0C 08 95 E8 94 09 C0 97 FB 3E F4 90 95 80 95 70 95 61 95 7F 4F 8F 4F 9F 4F 99 23 A9 F0 F9 2F 96 E9 BB 27 
3430 1731542539196 pro JtagIce3 [0x12] >>> 80 00 
3430 1731542539196 pro JtagIce3 [0x12] <<< 23 00 C0 80 06 00 00 80 00 00 00 00 93 95 F6 95 87 95 77 95 67 95 B7 95 F1 11 F8 CF FA F4 BB 0F 11 F4 60 FF 1B C0 6F 5F 7F 4F 8F 4F 9F 4F 16 C0 88 23 11 F0 96 E9 11 C0 77 23 21 F0 9E E8 87 2F 76 2F 05 C0 66 23 71 F0 96 E8 86 2F 70 E0 60 E0 2A F0 9A 95 66 0F 77 1F 88 1F DA F7 88 0F 96 95 87 95 97 F9 08 95 E0 EA F4 E0 20 81 21 60 20 83 20 81 2D 7F 20 83 0E 94 30 03 20 E0 30 E0 40 E8 51 E4 0E 94 57 06 9B 01 AC 01 64 E5 
3430 1731542539214 pro JtagIce3 [0x12] >>> 80 00 
3430 1731542539214 pro JtagIce3 [0x12] <<< 23 00 C0 00 07 00 00 80 00 00 00 00 73 E7 8B E4 9D E4 0E 94 53 06 20 E0 30 E0 40 E0 5F E3 0E 94 0D 06 0E 94 9C 03 E0 E4 F8 E0 60 87 71 87 86 81 80 6C 86 83 83 E0 87 83 84 EF 9B E4 0E 94 3A 05 80 E0 08 95 0E 94 1A 04 88 F0 9F 57 98 F0 B9 2F 99 27 B7 51 B0 F0 E1 F0 66 0F 77 1F 88 1F 99 1F 1A F0 BA 95 C9 F7 14 C0 B1 30 91 F0 0E 94 21 06 B1 E0 08 95 0C 94 21 06 67 2F 78 2F 88 27 B8 5F 39 F0 B9 3F CC F3 86 95 77 95 67 95 
3430 1731542539232 pro JtagIce3 [0x12] >>> 80 00 
3430 1731542539232 pro JtagIce3 [0x12] <<< 23 00 C0 80 07 00 00 80 00 00 00 00 B3 95 D9 F7 3E F4 90 95 80 95 70 95 61 95 7F 4F 8F 4F 9F 4F 08 95 CF 93 C8 2F 86 E9 0E 94 C0 04 C2 31 70 F0 67 E8 8D E4 0E 94 51 05 C5 31 08 F0 C4 E1 C5 50 6C 2F 60 68 89 E0 0E 94 51 05 0D C0 C2 30 08 F4 C2 E0 64 E8 8D E4 0E 94 51 05 6E EF 6C 0F 60 68 89 E0 0E 94 51 05 CF 91 08 95 62 75 66 3A 20 00 0D 0A 00 6C 6F 72 61 20 63 6F 75 6C 64 20 6E 6F 74 20 69 6E 69 74 69 61 6C 69 73 65 
3430 1731542539250 pro JtagIce3 [0x12] >>> 80 00 
3430 1731542539250 pro JtagIce3 [0x12] <<< 23 00 C0 00 08 00 00 80 00 00 00 00 0D 0A 00 6C 6F 72 61 20 73 75 63 63 65 73 73 66 75 6C 6C 79 20 69 6E 69 74 69 61 6C 69 73 65 64 0D 0A 00 FF 57 FD 90 58 44 0F 55 1F 59 F0 5F 3F 71 F0 47 95 88 0F 97 FB 99 1F 61 F0 9F 3F 79 F0 87 95 08 95 12 16 13 06 14 06 55 1F F2 CF 46 95 F1 DF 08 C0 16 16 17 06 18 06 99 1F F1 CF 86 95 71 05 61 05 08 94 08 95 97 FB 10 F8 16 94 00 08 0F 93 08 30 98 F0 08 50 23 2F 34 2F 45 2F 56 2F 
3430 1731542539268 pro JtagIce3 [0x12] >>> 80 00 
3430 1731542539268 pro JtagIce3 [0x12] <<< 23 00 C0 80 08 00 00 80 00 00 00 00 67 2F 78 2F 89 2F 90 2D F4 CF 05 94 97 95 87 95 77 95 67 95 57 95 47 95 37 95 27 95 0A 95 AA F7 0F 91 08 95 1F 93 CF 93 DF 93 0F 92 CD B7 DE B7 18 2F BE 01 6F 5F 7F 4F 8D E1 0E 94 0C 05 69 81 6F 70 20 E1 12 9F C0 01 11 24 68 2B 8D E1 0E 94 51 05 0F 90 DF 91 CF 91 1F 91 08 95 1F 93 CF 93 DF 93 0F 92 CD B7 DE B7 18 2F BE 01 6F 5F 7F 4F 8E E1 0E 94 0C 05 69 81 6F 70 20 E1 12 9F C0 01 
3430 1731542539286 pro JtagIce3 [0x12] >>> 80 00 
3430 1731542539286 pro JtagIce3 [0x12] <<< 23 00 C0 00 09 00 00 80 00 00 00 00 11 24 68 2B 8E E1 0E 94 51 05 0F 90 DF 91 CF 91 1F 91 08 95 1F 93 CF 93 DF 93 0F 92 CD B7 DE B7 18 2F BE 01 6F 5F 7F 4F 8D E1 0E 94 0C 05 69 81 96 2F 91 7F 61 2F 66 0F 69 2B 8D E1 0E 94 51 05 0F 90 DF 91 CF 91 1F 91 08 95 60 E8 75 E2 80 E0 90 E0 0E 94 6D 03 0E 94 75 00 81 11 05 C0 87 EE 97 E4 0E 94 3A 05 FF CF 83 E0 98 E4 0E 94 3A 05 82 EA 95 E0 0E 94 44 06 78 94 0E 94 31 02 FD CF 
3430 1731542539304 pro JtagIce3 [0x12] >>> 80 00 
3430 1731542539304 pro JtagIce3 [0x12] <<< 23 00 C0 80 09 00 00 80 00 00 00 00 81 3F B0 F4 89 37 38 F4 90 E0 8D 97 65 E0 70 E0 0E 94 7A 05 06 C0 90 E0 4E 96 6A E0 70 E0 0E 94 7A 05 6F 71 60 62 8B E0 0E 94 51 05 81 E0 08 95 80 E0 08 95 E0 EC F8 E0 84 83 83 81 88 23 24 F4 0A C0 01 97 29 F4 0D C0 89 EE 93 E0 E0 EC F8 E0 23 81 22 23 B4 F7 80 91 C4 08 FB 01 80 83 80 E0 08 95 81 E0 08 95 0F 93 08 30 90 F0 98 2F 87 2F 76 2F 65 2F 54 2F 43 2F 32 2F 22 27 08 50 F4 CF 
3430 1731542539322 pro JtagIce3 [0x12] >>> 80 00 
3430 1731542539322 pro JtagIce3 [0x12] <<< 23 00 C0 00 0A 00 00 80 00 00 00 00 22 0F 33 1F 44 1F 55 1F 66 1F 77 1F 88 1F 99 1F 0A 95 B2 F7 0F 91 08 95 0F 93 1F 93 CF 93 C8 2F 8B 01 0E 94 28 06 8C 2F 8F 77 0E 94 C6 05 C8 2F C8 01 0E 94 4E 06 C8 2B 0E 94 2E 06 8C 2F CF 91 1F 91 0F 91 08 95 E0 E0 F4 E0 80 81 80 61 80 83 80 81 8F 7D 80 83 80 81 80 64 80 83 80 81 80 68 80 83 E0 EC F8 E0 81 E3 80 83 81 81 83 60 81 83 80 E0 08 95 0F 93 1F 93 CF 93 FC 01 80 81 88 23 
3430 1731542539340 pro JtagIce3 [0x12] >>> 80 00 
3430 1731542539340 pro JtagIce3 [0x12] <<< 23 00 C0 80 0A 00 00 80 00 00 00 00 59 F0 8F 01 C0 E0 0E 94 04 06 CF 5F F8 01 EC 0F F1 1D 80 81 81 11 F7 CF 80 E0 CF 91 1F 91 0F 91 08 95 CF 93 DF 93 C8 2F D6 2F 0E 94 28 06 8C 2F 80 68 0E 94 C6 05 C8 2F 8D 2F 0E 94 C6 05 C8 2B 0E 94 2E 06 8C 2F DF 91 CF 91 08 95 CF 93 DF 93 0F 92 CD B7 DE B7 BE 01 6F 5F 7F 4F 8D E1 0E 94 0C 05 69 81 6E 7F 8D E1 0E 94 51 05 0F 90 DF 91 CF 91 08 95 97 FB 07 2E 16 F4 00 94 07 D0 77 FD 
3430 1731542539358 pro JtagIce3 [0x12] >>> 80 00 
3430 1731542539358 pro JtagIce3 [0x12] <<< 23 00 C0 00 0B 00 00 80 00 00 00 00 09 D0 0E 94 8E 05 07 FC 05 D0 3E F4 90 95 81 95 9F 4F 08 95 70 95 61 95 7F 4F 08 95 AA 1B BB 1B 51 E1 07 C0 AA 1F BB 1F A6 17 B7 07 10 F0 A6 1B B7 0B 88 1F 99 1F 5A 95 A9 F7 80 95 90 95 BC 01 CD 01 08 95 CF 93 DF 93 40 32 61 F0 EC 01 8E ED 97 E4 0E 94 3A 05 CE 01 0E 94 3A 05 84 EE 97 E4 0E 94 3A 05 DF 91 CF 91 08 95 09 2E 03 94 00 0C 11 F4 88 23 52 F0 BB 0F 40 F4 BF 2B 11 F4 60 FF 
3430 1731542539376 pro JtagIce3 [0x12] >>> 80 00 
3430 1731542539376 pro JtagIce3 [0x12] <<< 23 00 C0 80 0B 00 00 80 00 00 00 00 04 C0 6F 5F 7F 4F 8F 4F 9F 4F 08 95 CF 93 DF 93 0F 92 CD B7 DE B7 BE 01 6F 5F 7F 4F 0E 94 DA 04 0F 90 DF 91 CF 91 08 95 68 94 01 C0 E8 94 8F 92 9F 92 CF 93 DF 93 0E 94 DF 02 DF 91 CF 91 9F 90 8F 90 08 95 8F 93 80 91 09 04 83 FF 06 C0 81 E0 80 93 01 31 88 E0 80 93 09 04 8F 91 18 95 EC 01 0E 94 63 06 0E 94 62 06 CE 01 0E 94 64 06 CE 01 0E 94 60 06 75 61 72 74 20 69 6E 69 74 69 61 6C 
3430 1731542539394 pro JtagIce3 [0x12] >>> 80 00 
3430 1731542539394 pro JtagIce3 [0x12] <<< 23 00 C0 00 0C 00 00 80 00 00 00 00 69 73 65 64 0D 0A 00 FF E0 E4 F8 E0 94 81 95 FF FD CF 80 93 42 08 08 95 50 58 BB 27 AA 27 0E 94 CA 01 0C 94 B5 05 00 24 0A 94 16 16 17 06 18 06 09 06 08 95 00 24 0A 94 12 16 13 06 14 06 05 06 08 95 E8 94 BB 27 66 27 77 27 CB 01 97 F9 08 95 E0 E0 F4 E0 84 81 8F 77 84 83 08 95 E0 E0 F4 E0 84 81 80 68 84 83 08 95 97 F9 9F 67 80 E8 70 E0 60 E0 08 95 60 E8 81 E0 0E 94 51 05 08 95 61 E8 
3430 1731542539412 pro JtagIce3 [0x12] >>> 80 00 
3430 1731542539412 pro JtagIce3 [0x12] <<< 23 00 C0 80 0C 00 00 80 00 00 00 00 81 E0 0E 94 51 05 08 95 80 93 FF 30 90 93 00 31 08 95 65 E8 81 E0 0E 94 51 05 08 95 BC 01 80 E0 0E 94 DA 04 08 95 0E 94 F1 00 0C 94 B5 05 0E 94 60 01 0C 94 B5 05 9F EF 80 EC 08 95 0C 94 00 00 0E 94 73 00 08 95 08 95 08 95 FF FF FF FF FF FF FF FF FF FF FF FF FF FF FF FF FF FF FF FF FF FF FF FF FF FF FF FF FF FF FF FF FF FF FF FF FF FF FF FF FF FF FF FF FF FF FF FF FF FF FF FF FF FF 
3430 1731542539430 pro JtagIce3 [0x12] >>> 80 00 
3430 1731542539430 pro JtagIce3 [0x12] <<< 21 00 C0 00 00 00 00 80 00 00 00 
3430 1731542539440 pro JtagIce3 [0x12] >>> 84 00 0C 94 4B 00 0C 94 5E 06 0C 94 5E 06 0C 94 5E 06 0C 94 5E 06 0C 94 5E 06 0C 94 E2 05 0C 94 5E 06 0C 94 5E 06 0C 94 5E 06 0C 94 5E 06 0C 94 5E 06 0C 94 5E 06 0C 94 5E 06 0C 94 5E 06 0C 94 5E 06 0C 94 5E 06 0C 94 5E 06 0C 94 5E 06 0C 94 5E 06 0C 94 5E 06 0C 94 5E 06 0C 94 5E 06 0C 94 5E 06 0C 94 5E 06 0C 94 5E 06 0C 94 5E 06 0C 94 5E 06 0C 94 5E 06 0C 94 5E 06 0C 94 5E 06 0C 94 5E 06 00 
3430 1731542539440 pro JtagIce3 [0x12] <<< 21 00 C0 80 00 00 00 80 00 00 00 
3430 1731542539449 pro JtagIce3 [0x12] >>> 84 00 0C 94 5E 06 0C 94 5E 06 0C 94 5E 06 0C 94 5E 06 30 00 31 02 80 00 11 24 1F BE CF EF CD BF DF E3 DE BF E0 E9 F0 E0 40 E0 17 C0 B5 91 A5 91 35 91 25 91 05 91 07 FD 0C C0 95 91 85 91 EF 01 F9 2F E8 2F 05 90 0D 92 A2 17 B3 07 D9 F7 FE 01 04 C0 1D 92 A2 17 B3 07 E1 F7 E5 39 F4 07 31 F7 0E 94 A5 04 0C 94 EF 05 F8 94 FF CF CF 93 DF 93 00 D0 CD B7 DE B7 0E 94 23 05 E0 E0 F4 E0 81 81 84 60 00 
3430 1731542539449 pro JtagIce3 [0x12] <<< 21 00 C0 00 01 00 00 80 00 00 00 
3430 1731542539459 pro JtagIce3 [0x12] >>> 84 00 81 83 81 81 87 7F 81 83 83 89 82 60 83 8B 84 81 84 60 84 83 82 EC 92 EA 01 97 F1 F7 00 C0 84 81 8B 7F 84 83 81 E4 93 E0 01 97 F1 F7 00 00 84 81 84 60 84 83 8D E8 90 E2 01 97 F1 F7 00 00 0E 94 2E 06 BE 01 6F 5F 7F 4F 82 E4 0E 94 0C 05 89 81 82 31 09 F0 40 C0 0E 94 3A 06 60 E8 81 E0 0E 94 51 05 60 E4 7E E0 8F EC 99 E1 0E 94 8A 02 60 E0 8E E0 0E 94 51 05 60 E0 8F E0 0E 94 51 05 BE 01 00 
3430 1731542539459 pro JtagIce3 [0x12] <<< 21 00 C0 80 01 00 00 80 00 00 00 
3430 1731542539469 pro JtagIce3 [0x12] >>> 84 00 6E 5F 7F 4F 8C E0 0E 94 0C 05 6A 81 63 60 8C E0 0E 94 51 05 64 E0 86 E2 0E 94 51 05 60 E0 80 E4 0E 94 51 05 87 E0 0E 94 52 04 87 E0 0E 94 6E 04 81 E0 0E 94 8A 04 84 E1 0E 94 CB 03 0E 94 66 05 0E 94 3F 06 82 EC 92 EA 01 97 F1 F7 00 C0 0E 94 49 06 80 E0 01 C0 81 E0 0F 90 0F 90 DF 91 CF 91 08 95 10 C0 0E 94 1A 06 58 F0 0E 94 13 06 40 F0 29 F4 5F 3F 29 F0 0C 94 34 06 51 11 0C 94 22 06 00 
3430 1731542539469 pro JtagIce3 [0x12] <<< 21 00 C0 00 02 00 00 80 00 00 00 
3430 1731542539479 pro JtagIce3 [0x12] >>> 84 00 0C 94 5B 06 0E 94 12 04 68 F3 99 23 B1 F3 55 23 91 F3 95 1B 55 0B BB 27 AA 27 62 17 73 07 84 07 38 F0 9F 5F 5F 4F 22 0F 33 1F 44 1F AA 1F A9 F3 35 D0 0E 2E 3A F0 E0 E8 32 D0 91 50 50 40 E6 95 00 1C CA F7 2B D0 FE 2F 29 D0 66 0F 77 1F 88 1F BB 1F 26 17 37 07 48 07 AB 07 B0 E8 09 F0 BB 0B 80 2D BF 01 FF 27 93 58 5F 4F 3A F0 9E 3F 51 05 78 F0 0C 94 34 06 0C 94 22 06 5F 3F E4 F3 98 3E 00 
3430 1731542539479 pro JtagIce3 [0x12] <<< 21 00 C0 80 02 00 00 80 00 00 00 
3430 1731542539489 pro JtagIce3 [0x12] >>> 84 00 D4 F3 86 95 77 95 67 95 B7 95 F7 95 9F 5F C9 F7 88 0F 91 1D 96 95 87 95 97 F9 08 95 E1 E0 66 0F 77 1F 88 1F BB 1F 62 17 73 07 84 07 BA 07 20 F0 62 1B 73 0B 84 0B BA 0B EE 1F 88 F7 E0 95 08 95 0F C0 0E 94 13 06 38 F0 0E 94 1A 06 20 F0 95 23 11 F0 0C 94 34 06 0C 94 5B 06 11 24 0C 94 22 06 0E 94 12 04 70 F3 95 9F C1 F3 95 0F 50 E0 55 1F 62 9F F0 01 72 9F BB 27 F0 0D B1 1D 63 9F AA 27 00 
3430 1731542539489 pro JtagIce3 [0x12] <<< 21 00 C0 00 03 00 00 80 00 00 00 
3430 1731542539499 pro JtagIce3 [0x12] >>> 84 00 F0 0D B1 1D AA 1F 64 9F 66 27 B0 0D A1 1D 66 1F 82 9F 22 27 B0 0D A1 1D 62 1F 73 9F B0 0D A1 1D 62 1F 83 9F A0 0D 61 1D 22 1F 74 9F 33 27 A0 0D 61 1D 23 1F 84 9F 60 0D 21 1D 82 2F 76 2F 6A 2F 11 24 9F 57 50 40 9A F0 F1 F0 88 23 4A F0 EE 0F FF 1F BB 1F 66 1F 77 1F 88 1F 91 50 50 40 A9 F7 9E 3F 51 05 80 F0 0C 94 34 06 0C 94 22 06 5F 3F E4 F3 98 3E D4 F3 86 95 77 95 67 95 B7 95 F7 95 00 
3430 1731542539499 pro JtagIce3 [0x12] <<< 21 00 C0 80 03 00 00 80 00 00 00 
3430 1731542539509 pro JtagIce3 [0x12] >>> 84 00 E7 95 9F 5F C1 F7 FE 2B 88 0F 91 1D 96 95 87 95 97 F9 08 95 11 C0 0E 94 13 06 38 F0 0E 94 1A 06 20 F0 39 F4 9F 3F 19 F4 26 F4 0C 94 5B 06 0E F4 E0 95 E7 FB 0C 94 34 06 E9 2F 0E 94 12 04 58 F3 BA 17 62 07 73 07 84 07 95 07 20 F0 79 F4 A6 F5 0C 94 21 06 0E F4 E0 95 0B 2E BA 2F A0 2D 0B 01 B9 01 90 01 0C 01 CA 01 A0 01 11 24 FF 27 59 1B 99 F0 59 3F 50 F4 50 3E 68 F1 1A 16 F0 40 A2 2F 00 
3430 1731542539509 pro JtagIce3 [0x12] <<< 21 00 C0 00 04 00 00 80 00 00 00 
3430 1731542539519 pro JtagIce3 [0x12] >>> 84 00 23 2F 34 2F 44 27 58 5F F3 CF 46 95 37 95 27 95 A7 95 F0 40 53 95 C9 F7 7E F4 1F 16 BA 0B 62 0B 73 0B 84 0B BA F0 91 50 A1 F0 FF 0F BB 1F 66 1F 77 1F 88 1F C2 F7 0E C0 BA 0F 62 1F 73 1F 84 1F 48 F4 87 95 77 95 67 95 B7 95 F7 95 9E 3F 08 F0 B0 CF 93 95 88 0F 08 F0 99 27 EE 0F 97 95 87 95 08 95 1F 93 CF 93 DF 93 00 D0 0F 92 CD B7 DE B7 80 91 01 31 88 23 09 F4 46 C0 BE 01 6E 5F 7F 4F 00 
3430 1731542539519 pro JtagIce3 [0x12] <<< 21 00 C0 80 04 00 00 80 00 00 00 
3430 1731542539529 pro JtagIce3 [0x12] >>> 84 00 82 E1 0E 94 0C 05 6A 81 82 E1 0E 94 51 05 8A 81 85 FF 0C C0 E0 91 FF 30 F0 91 00 31 30 97 89 F1 40 E2 60 E0 80 E0 90 E0 09 95 2B C0 86 FF 29 C0 BE 01 6D 5F 7F 4F 83 E1 0E 94 0C 05 BE 01 6F 5F 7F 4F 80 E1 0E 94 0C 05 69 81 8D E0 0E 94 51 05 6B 81 66 23 61 F0 10 E0 61 2F 70 E0 60 50 70 4D 80 E0 0E 94 0C 05 1F 5F 6B 81 16 17 A8 F3 E0 91 FF 30 F0 91 00 31 30 97 21 F0 40 E4 80 E0 90 E3 00 
3430 1731542539529 pro JtagIce3 [0x12] <<< 21 00 C0 00 05 00 00 80 00 00 00 
3430 1731542539539 pro JtagIce3 [0x12] >>> 84 00 09 95 10 92 01 31 23 96 CD BF DE BF DF 91 CF 91 1F 91 08 95 AF 92 BF 92 CF 92 DF 92 EF 92 FF 92 0F 93 1F 93 CF 93 DF 93 DC 01 CB 01 28 2F 39 2F 4A 2F 5B 2F 60 E0 70 E0 80 E0 90 E0 03 E1 0E 94 F3 04 A1 2C 0F 2E F8 E4 BF 2E F0 2D 0F 2E F8 EE CF 2E F0 2D DD 24 D3 94 E1 2C F1 2C 00 E0 10 E0 0E 94 D6 05 C2 2F B3 2E C4 2E D5 2E E6 2E F7 2E 18 2F D9 2F 00 E1 0E 94 36 04 62 2F 86 E0 0E 94 00 
3430 1731542539539 pro JtagIce3 [0x12] <<< 21 00 C0 80 05 00 00 80 00 00 00 
3430 1731542539549 pro JtagIce3 [0x12] >>> 84 00 51 05 2C 2F 3B 2D 4C 2D 5D 2D 6E 2D 7F 2D 81 2F 9D 2F 08 E0 0E 94 36 04 62 2F 87 E0 0E 94 51 05 6C 2F 88 E0 0E 94 51 05 DF 91 CF 91 1F 91 0F 91 FF 90 EF 90 DF 90 CF 90 BF 90 AF 90 08 95 88 24 99 24 F4 01 E4 01 B0 E4 9F 93 AA 27 9A 15 8B 04 9C 04 ED 05 FE 05 CF 05 D0 07 A1 07 98 F4 AD 2F DC 2F CF 2F FE 2F E9 2D 98 2C 89 2E 98 2F 87 2F 76 2F 65 2F 54 2F 43 2F 32 2F 22 27 B8 50 31 F7 00 
3430 1731542539549 pro JtagIce3 [0x12] <<< 21 00 C0 00 06 00 00 80 00 00 00 
3430 1731542539559 pro JtagIce3 [0x12] >>> 84 00 BF 91 27 C0 1B 2E BF 91 BB 27 22 0F 33 1F 44 1F 55 1F 66 1F 77 1F 88 1F 99 1F 88 1C 99 1C EE 1F FF 1F CC 1F DD 1F AA 1F BB 1F 8A 14 9B 04 EC 05 FD 05 CE 05 DF 05 A0 07 B1 07 48 F0 8A 18 9B 08 EC 09 FD 09 CE 09 DF 09 A0 0B B1 0B 21 60 1A 94 E1 F6 2E F4 94 01 AF 01 BE 01 CD 01 00 0C 08 95 E8 94 09 C0 97 FB 3E F4 90 95 80 95 70 95 61 95 7F 4F 8F 4F 9F 4F 99 23 A9 F0 F9 2F 96 E9 BB 27 00 
3430 1731542539559 pro JtagIce3 [0x12] <<< 21 00 C0 80 06 00 00 80 00 00 00 
3430 1731542539569 pro JtagIce3 [0x12] >>> 84 00 93 95 F6 95 87 95 77 95 67 95 B7 95 F1 11 F8 CF FA F4 BB 0F 11 F4 60 FF 1B C0 6F 5F 7F 4F 8F 4F 9F 4F 16 C0 88 23 11 F0 96 E9 11 C0 77 23 21 F0 9E E8 87 2F 76 2F 05 C0 66 23 71 F0 96 E8 86 2F 70 E0 60 E0 2A F0 9A 95 66 0F 77 1F 88 1F DA F7 88 0F 96 95 87 95 97 F9 08 95 E0 EA F4 E0 20 81 21 60 20 83 20 81 2D 7F 20 83 0E 94 30 03 20 E0 30 E0 40 E8 51 E4 0E 94 57 06 9B 01 AC 01 64 E5 00 
3430 1731542539569 pro JtagIce3 [0x12] <<< 21 00 C0 00 07 00 00 80 00 00 00 
3430 1731542539579 pro JtagIce3 [0x12] >>> 84 00 73 E7 8B E4 9D E4 0E 94 53 06 20 E0 30 E0 40 E0 5F E3 0E 94 0D 06 0E 94 9C 03 E0 E4 F8 E0 60 87 71 87 86 81 80 6C 86 83 83 E0 87 83 84 EF 9B E4 0E 94 3A 05 80 E0 08 95 0E 94 1A 04 88 F0 9F 57 98 F0 B9 2F 99 27 B7 51 B0 F0 E1 F0 66 0F 77 1F 88 1F 99 1F 1A F0 BA 95 C9 F7 14 C0 B1 30 91 F0 0E 94 21 06 B1 E0 08 95 0C 94 21 06 67 2F 78 2F 88 27 B8 5F 39 F0 B9 3F CC F3 86 95 77 95 67 95 00 
3430 1731542539579 pro JtagIce3 [0x12] <<< 21 00 C0 80 07 00 00 80 00 00 00 
3430 1731542539589 pro JtagIce3 [0x12] >>> 84 00 B3 95 D9 F7 3E F4 90 95 80 95 70 95 61 95 7F 4F 8F 4F 9F 4F 08 95 CF 93 C8 2F 86 E9 0E 94 C0 04 C2 31 70 F0 67 E8 8D E4 0E 94 51 05 C5 31 08 F0 C4 E1 C5 50 6C 2F 60 68 89 E0 0E 94 51 05 0D C0 C2 30 08 F4 C2 E0 64 E8 8D E4 0E 94 51 05 6E EF 6C 0F 60 68 89 E0 0E 94 51 05 CF 91 08 95 62 75 66 3A 20 00 0D 0A 00 6C 6F 72 61 20 63 6F 75 6C 64 20 6E 6F 74 20 69 6E 69 74 69 61 6C 69 73 65 00 
3430 1731542539589 pro JtagIce3 [0x12] <<< 21 00 C0 00 08 00 00 80 00 00 00 
3430 1731542539599 pro JtagIce3 [0x12] >>> 84 00 0D 0A 00 6C 6F 72 61 20 73 75 63 63 65 73 73 66 75 6C 6C 79 20 69 6E 69 74 69 61 6C 69 73 65 64 0D 0A 00 FF 57 FD 90 58 44 0F 55 1F 59 F0 5F 3F 71 F0 47 95 88 0F 97 FB 99 1F 61 F0 9F 3F 79 F0 87 95 08 95 12 16 13 06 14 06 55 1F F2 CF 46 95 F1 DF 08 C0 16 16 17 06 18 06 99 1F F1 CF 86 95 71 05 61 05 08 94 08 95 97 FB 10 F8 16 94 00 08 0F 93 08 30 98 F0 08 50 23 2F 34 2F 45 2F 56 2F 00 
3430 1731542539599 pro JtagIce3 [0x12] <<< 21 00 C0 80 08 00 00 80 00 00 00 
3430 1731542539609 pro JtagIce3 [0x12] >>> 84 00 67 2F 78 2F 89 2F 90 2D F4 CF 05 94 97 95 87 95 77 95 67 95 57 95 47 95 37 95 27 95 0A 95 AA F7 0F 91 08 95 1F 93 CF 93 DF 93 0F 92 CD B7 DE B7 18 2F BE 01 6F 5F 7F 4F 8D E1 0E 94 0C 05 69 81 6F 70 20 E1 12 9F C0 01 11 24 68 2B 8D E1 0E 94 51 05 0F 90 DF 91 CF 91 1F 91 08 95 1F 93 CF 93 DF 93 0F 92 CD B7 DE B7 18 2F BE 01 6F 5F 7F 4F 8E E1 0E 94 0C 05 69 81 6F 70 20 E1 12 9F C0 01 00 
3430 1731542539609 pro JtagIce3 [0x12] <<< 21 00 C0 00 09 00 00 80 00 00 00 
3430 1731542539618 pro JtagIce3 [0x12] >>> 84 00 11 24 68 2B 8E E1 0E 94 51 05 0F 90 DF 91 CF 91 1F 91 08 95 1F 93 CF 93 DF 93 0F 92 CD B7 DE B7 18 2F BE 01 6F 5F 7F 4F 8D E1 0E 94 0C 05 69 81 96 2F 91 7F 61 2F 66 0F 69 2B 8D E1 0E 94 51 05 0F 90 DF 91 CF 91 1F 91 08 95 60 E8 75 E2 80 E0 90 E0 0E 94 6D 03 0E 94 75 00 81 11 05 C0 87 EE 97 E4 0E 94 3A 05 FF CF 83 E0 98 E4 0E 94 3A 05 82 EA 95 E0 0E 94 44 06 78 94 0E 94 31 02 FD CF 00 
3430 1731542539618 pro JtagIce3 [0x12] <<< 21 00 C0 80 09 00 00 80 00 00 00 
3430 1731542539628 pro JtagIce3 [0x12] >>> 84 00 81 3F B0 F4 89 37 38 F4 90 E0 8D 97 65 E0 70 E0 0E 94 7A 05 06 C0 90 E0 4E 96 6A E0 70 E0 0E 94 7A 05 6F 71 60 62 8B E0 0E 94 51 05 81 E0 08 95 80 E0 08 95 E0 EC F8 E0 84 83 83 81 88 23 24 F4 0A C0 01 97 29 F4 0D C0 89 EE 93 E0 E0 EC F8 E0 23 81 22 23 B4 F7 80 91 C4 08 FB 01 80 83 80 E0 08 95 81 E0 08 95 0F 93 08 30 90 F0 98 2F 87 2F 76 2F 65 2F 54 2F 43 2F 32 2F 22 27 08 50 F4 CF 00 
3430 1731542539628 pro JtagIce3 [0x12] <<< 21 00 C0 00 0A 00 00 80 00 00 00 
3430 1731542539637 pro JtagIce3 [0x12] >>> 84 00 22 0F 33 1F 44 1F 55 1F 66 1F 77 1F 88 1F 99 1F 0A 95 B2 F7 0F 91 08 95 0F 93 1F 93 CF 93 C8 2F 8B 01 0E 94 28 06 8C 2F 8F 77 0E 94 C6 05 C8 2F C8 01 0E 94 4E 06 C8 2B 0E 94 2E 06 8C 2F CF 91 1F 91 0F 91 08 95 E0 E0 F4 E0 80 81 80 61 80 83 80 81 8F 7D 80 83 80 81 80 64 80 83 80 81 80 68 80 83 E0 EC F8 E0 81 E3 80 83 81 81 83 60 81 83 80 E0 08 95 0F 93 1F 93 CF 93 FC 01 80 81 88 23 00 
3430 1731542539637 pro JtagIce3 [0x12] <<< 21 00 C0 80 0A 00 00 80 00 00 00 
3430 1731542539647 pro JtagIce3 [0x12] >>> 84 00 59 F0 8F 01 C0 E0 0E 94 04 06 CF 5F F8 01 EC 0F F1 1D 80 81 81 11 F7 CF 80 E0 CF 91 1F 91 0F 91 08 95 CF 93 DF 93 C8 2F D6 2F 0E 94 28 06 8C 2F 80 68 0E 94 C6 05 C8 2F 8D 2F 0E 94 C6 05 C8 2B 0E 94 2E 06 8C 2F DF 91 CF 91 08 95 CF 93 DF 93 0F 92 CD B7 DE B7 BE 01 6F 5F 7F 4F 8D E1 0E 94 0C 05 69 81 6E 7F 8D E1 0E 94 51 05 0F 90 DF 91 CF 91 08 95 97 FB 07 2E 16 F4 00 94 07 D0 77 FD 00 
3430 1731542539647 pro JtagIce3 [0x12] <<< 21 00 C0 00 0B 00 00 80 00 00 00 
3430 1731542539656 pro JtagIce3 [0x12] >>> 84 00 09 D0 0E 94 8E 05 07 FC 05 D0 3E F4 90 95 81 95 9F 4F 08 95 70 95 61 95 7F 4F 08 95 AA 1B BB 1B 51 E1 07 C0 AA 1F BB 1F A6 17 B7 07 10 F0 A6 1B B7 0B 88 1F 99 1F 5A 95 A9 F7 80 95 90 95 BC 01 CD 01 08 95 CF 93 DF 93 40 32 61 F0 EC 01 8E ED 97 E4 0E 94 3A 05 CE 01 0E 94 3A 05 84 EE 97 E4 0E 94 3A 05 DF 91 CF 91 08 95 09 2E 03 94 00 0C 11 F4 88 23 52 F0 BB 0F 40 F4 BF 2B 11 F4 60 FF 00 
3430 1731542539656 pro JtagIce3 [0x12] <<< 21 00 C0 80 0B 00 00 80 00 00 00 
3430 1731542539666 pro JtagIce3 [0x12] >>> 84 00 04 C0 6F 5F 7F 4F 8F 4F 9F 4F 08 95 CF 93 DF 93 0F 92 CD B7 DE B7 BE 01 6F 5F 7F 4F 0E 94 DA 04 0F 90 DF 91 CF 91 08 95 68 94 01 C0 E8 94 8F 92 9F 92 CF 93 DF 93 0E 94 DF 02 DF 91 CF 91 9F 90 8F 90 08 95 8F 93 80 91 09 04 83 FF 06 C0 81 E0 80 93 01 31 88 E0 80 93 09 04 8F 91 18 95 EC 01 0E 94 63 06 0E 94 62 06 CE 01 0E 94 64 06 CE 01 0E 94 60 06 75 61 72 74 20 69 6E 69 74 69 61 6C 00 
3430 1731542539666 pro JtagIce3 [0x12] <<< 21 00 C0 00 0C 00 00 80 00 00 00 
3430 1731542539676 pro JtagIce3 [0x12] >>> 84 00 69 73 65 64 0D 0A 00 FF E0 E4 F8 E0 94 81 95 FF FD CF 80 93 42 08 08 95 50 58 BB 27 AA 27 0E 94 CA 01 0C 94 B5 05 00 24 0A 94 16 16 17 06 18 06 09 06 08 95 00 24 0A 94 12 16 13 06 14 06 05 06 08 95 E8 94 BB 27 66 27 77 27 CB 01 97 F9 08 95 E0 E0 F4 E0 84 81 8F 77 84 83 08 95 E0 E0 F4 E0 84 81 80 68 84 83 08 95 97 F9 9F 67 80 E8 70 E0 60 E0 08 95 60 E8 81 E0 0E 94 51 05 08 95 61 E8 00 
3430 1731542539676 pro JtagIce3 [0x12] <<< 21 00 C0 80 0C 00 00 80 00 00 00 
3430 1731542539686 pro JtagIce3 [0x12] >>> 84 00 81 E0 0E 94 51 05 08 95 80 93 FF 30 90 93 00 31 08 95 65 E8 81 E0 0E 94 51 05 08 95 BC 01 80 E0 0E 94 DA 04 08 95 0E 94 F1 00 0C 94 B5 05 0E 94 60 01 0C 94 B5 05 9F EF 80 EC 08 95 0C 94 00 00 0E 94 73 00 08 95 08 95 08 95 FF FF FF FF FF FF FF FF FF FF FF FF FF FF FF FF FF FF FF FF FF FF FF FF FF FF FF FF FF FF FF FF FF FF FF FF FF FF FF FF FF FF FF FF FF FF FF FF FF FF FF FF FF FF 00 
3430 1731542539686 GEN4_TO_CONTROLLER_LOG:GEN4_PROGRAM_INT_LOG_ATmega3208 Post:SendOperation
3430 1731542539686 GEN4_TO_CONTROLLER_LOG:GEN4_PROGRAM_INT_LOG_ATmega3208 Return Value
3430 1731542539686 GEN4_TO_CONTROLLER_LOG:GEN4_PROGRAM_INT_LOG_ATmega3208 None
3430 1731542539686 GEN4_TO_CONTROLLER_LOG:GEN4_PROGRAM_INT_LOG_ATmega3208 Return End

3430 1731542539686 GEN4_TO_CONTROLLER_LOG:GEN4_PROGRAM_INT_LOG_ATmega3208 Pre:endOfOperations
3430 1731542539686 GEN4_TO_CONTROLLER_LOG:GEN4_PROGRAM_INT_LOG_ATmega3208 Payload
3430 1731542539686 GEN4_TO_CONTROLLER_LOG:GEN4_PROGRAM_INT_LOG_ATmega3208 null
3430 1731542539686 GEN4_TO_CONTROLLER_LOG:GEN4_PROGRAM_INT_LOG_ATmega3208 Payload End
3430 1731542539686 pro JtagIce3 [0x12] <<< 16 00 
3430 1731542539690 pro JtagIce3 [0x12] >>> 80 00 
3430 1731542539690 pro JtagIce3 [0x12] <<< 11 00 
3430 1731542539694 pro JtagIce3 [0x12] >>> 80 00 
3430 1731542539694 pro JtagIce3 [0x01] <<< 11 00 00 
3430 1731542539698 pro JtagIce3 [0x01] >>> 80 00 
3430 1731542539698 GEN4_TO_CONTROLLER_LOG:GEN4_PROGRAM_INT_LOG_ATmega3208 Post:endOfOperations
3430 1731542539698 GEN4_TO_CONTROLLER_LOG:GEN4_PROGRAM_INT_LOG_ATmega3208 Return Value
3430 1731542539698 GEN4_TO_CONTROLLER_LOG:GEN4_PROGRAM_INT_LOG_ATmega3208 None
3430 1731542539698 GEN4_TO_CONTROLLER_LOG:GEN4_PROGRAM_INT_LOG_ATmega3208 Return End

3430 1731542539699 GEN4_TO_CONTROLLER_LOG:GEN4_PROGRAM_INT_LOG_ATmega3208 Pre:SendOperation
3430 1731542539699 GEN4_TO_CONTROLLER_LOG:GEN4_PROGRAM_INT_LOG_ATmega3208 Payload
3430 1731542539699 GEN4_TO_CONTROLLER_LOG:GEN4_PROGRAM_INT_LOG_ATmega3208 OperationInfo: Values:
3430 1731542539699 GEN4_TO_CONTROLLER_LOG:GEN4_PROGRAM_INT_LOG_ATmega3208 OperationInfo: Type = releasefromreset, Mask = 00000000, Erase = false, Production Mode = true
3430 1731542539699 GEN4_TO_CONTROLLER_LOG:GEN4_PROGRAM_INT_LOG_ATmega3208 Payload End
3430 1731542539699 pro JtagIce3 [0x01] <<< 11 00 00 
3430 1731542539703 pro JtagIce3 [0x01] >>> 80 00 
3430 1731542539703 GEN4_TO_CONTROLLER_LOG:GEN4_PROGRAM_INT_LOG_ATmega3208 Post:SendOperation
3430 1731542539703 GEN4_TO_CONTROLLER_LOG:GEN4_PROGRAM_INT_LOG_ATmega3208 Return Value
3430 1731542539703 GEN4_TO_CONTROLLER_LOG:GEN4_PROGRAM_INT_LOG_ATmega3208 None
3430 1731542539703 GEN4_TO_CONTROLLER_LOG:GEN4_PROGRAM_INT_LOG_ATmega3208 Return End
3430 1731542539703 GEN4_CONNECT_DIAGNOSTICS:MPLABCommTool is null

3430 1731542539703 GEN4_TO_CONTROLLER_LOG:GEN4_CONNECT_INT_LOG Pre:GetFirmwareInfo
3430 1731542539703 GEN4_TO_CONTROLLER_LOG:GEN4_CONNECT_INT_LOG Payload
3430 1731542539703 GEN4_TO_CONTROLLER_LOG:GEN4_CONNECT_INT_LOG null
3430 1731542539703 GEN4_TO_CONTROLLER_LOG:GEN4_CONNECT_INT_LOG Payload End
3430 1731542539703 NativeController::GetFirmwareInfo entry
3430 1731542539704 pro JtagIce3 [0x01] <<< 02 00 00 00 01 
3430 1731542539707 pro JtagIce3 [0x01] >>> 84 01 00 00 
3430 1731542539707 NativeController::getFirmwareVersion entry
3430 1731542539707 pro JtagIce3 [0x01] <<< 02 00 00 01 01 
3430 1731542539711 pro JtagIce3 [0x01] >>> 84 01 01 00 
3430 1731542539711 pro JtagIce3 [0x01] <<< 02 00 00 02 01 
3430 1731542539715 pro JtagIce3 [0x01] >>> 84 01 1E 00 
3430 1731542539715 pro JtagIce3 [0x01] <<< 02 00 00 03 02 
3430 1731542539719 pro JtagIce3 [0x01] >>> 84 01 23 00 00 
3430 1731542539719 NativeController::getFirmwareVersion exit
3430 1731542539719 pro JtagIce3 [0x01] <<< 02 00 00 09 01 
3430 1731542539723 pro JtagIce3 [0x01] >>> 84 01 00 11 
3430 1731542539723 NativeController::tryGetFPGAVersion entry
3430 1731542539723 pro JtagIce3 [0x01] <<< 02 00 00 10 01 
3430 1731542539727 pro JtagIce3 [0x01] >>> 84 01 00 11 
3430 1731542539727 pro JtagIce3 [0x01] <<< 02 00 00 11 01 
3430 1731542539731 pro JtagIce3 [0x01] >>> 84 01 00 11 
3430 1731542539731 pro JtagIce3 [0x01] <<< 02 00 00 12 01 
3430 1731542539735 pro JtagIce3 [0x01] >>> 84 01 00 11 
3430 1731542539735 NativeController::tryGetFPGAVersion exit
3430 1731542539735 NativeController::tryGetFPGAVersion exit with exception No value present
3430 1731542539735 pro JtagIce3 [0x01] <<< 02 00 00 06 01 
3430 1731542539739 pro JtagIce3 [0x01] >>> 84 01 00 00 
3430 1731542539739 pro JtagIce3 [0x01] <<< 02 00 00 07 01 
3430 1731542539743 pro JtagIce3 [0x01] >>> 84 01 00 00 
3430 1731542539743 pro JtagIce3 [0x01] <<< 02 00 00 0A 01 
3430 1731542539747 pro JtagIce3 [0x01] >>> 84 01 00 00 
3430 1731542539747 NativeController::GetFirmwareInfo exit
3430 1731542539747 GEN4_TO_CONTROLLER_LOG:GEN4_CONNECT_INT_LOG Post:GetFirmwareInfo
3430 1731542539747 GEN4_TO_CONTROLLER_LOG:GEN4_CONNECT_INT_LOG Return Value
3430 1731542539747 GEN4_TO_CONTROLLER_LOG:GEN4_CONNECT_INT_LOG FirmwareInfo: Values:
3430 1731542539747 GEN4_TO_CONTROLLER_LOG:GEN4_CONNECT_INT_LOG FirmwareInfo: boot = false, bootVer = 0.0.0 (0x00.0x00.0x00), apVer = 1.30.35 (0x01.0x1e.0x23), fpgaVer = null, scriptVer = null, macAddress = , devID = 0, devID1 = 0, devSN0 = 0, devSN1 = 0, serialNumber = null, appCommitID = null, scriptCommitID = null, PCB_ID = 0
3430 1731542539747 GEN4_TO_CONTROLLER_LOG:GEN4_CONNECT_INT_LOG Return End

3430 1731542539747 GEN4_TO_CONTROLLER_LOG:GEN4_CONNECT_INT_LOG Pre:SetPowerInfo
3430 1731542539747 GEN4_TO_CONTROLLER_LOG:GEN4_CONNECT_INT_LOG Payload
3430 1731542539747 GEN4_TO_CONTROLLER_LOG:GEN4_CONNECT_INT_LOG PowerInfo: Values:
3430 1731542539747 GEN4_TO_CONTROLLER_LOG:GEN4_CONNECT_INT_LOG PowerInfo: shotDownSystem = true, isToolPower = false, voltage = 0,000000, useVppFirst = false, useLowVoltageProgramming = true, useMaintainActivePower = false
3430 1731542539747 GEN4_TO_CONTROLLER_LOG:GEN4_CONNECT_INT_LOG Payload End
3430 1731542539747 NativeController::GetVoltageInfo entry
3430 1731542539747 pro JtagIce3 [0x01] <<< 02 00 01 00 02 
3430 1731542539751 pro JtagIce3 [0x01] >>> 84 01 E2 0C 00 
3430 1731542539751 pro JtagIce3 [0x01] <<< 02 00 01 20 02 
3430 1731542539755 pro JtagIce3 [0x01] >>> 84 01 E4 0C 00 
3430 1731542539755 pro JtagIce3 [0x01] <<< 02 00 01 02 02 
3430 1731542539759 pro JtagIce3 [0x01] >>> 84 01 0B 00 00 
3430 1731542539759 NativeController::GetVoltageInfo exit
3430 1731542539759 GEN4_TO_CONTROLLER_LOG:GEN4_CONNECT_INT_LOG Post:SetPowerInfo
3430 1731542539759 GEN4_TO_CONTROLLER_LOG:GEN4_CONNECT_INT_LOG Return Value
3430 1731542539759 GEN4_TO_CONTROLLER_LOG:GEN4_CONNECT_INT_LOG none
3430 1731542539759 GEN4_TO_CONTROLLER_LOG:GEN4_CONNECT_INT_LOG Return End

3430 1731542539759 GEN4_TO_CONTROLLER_LOG:GEN4_CONNECT_INT_LOG Pre:Disconnect
3430 1731542539759 GEN4_TO_CONTROLLER_LOG:GEN4_CONNECT_INT_LOG Payload
3430 1731542539759 GEN4_TO_CONTROLLER_LOG:GEN4_CONNECT_INT_LOG Payload End
3430 1731542539759 NativeController::Disconnect entry
3430 1731542539759 pro JtagIce3 [0x01] <<< 11 00 00 
3430 1731542539763 pro JtagIce3 [0x01] >>> 80 00 
3430 1731542539763 NativeController::Disconnect exit
3430 1731542539763 GEN4_TO_CONTROLLER_LOG:GEN4_CONNECT_INT_LOG Post:Disconnect
3430 1731542539763 GEN4_TO_CONTROLLER_LOG:GEN4_CONNECT_INT_LOG Return Value
3430 1731542539763 GEN4_TO_CONTROLLER_LOG:GEN4_CONNECT_INT_LOG none
3430 1731542539763 GEN4_TO_CONTROLLER_LOG:GEN4_CONNECT_INT_LOG Return End
3430 1731542539763 GEN4_CONNECT_DIAGNOSTICS:Removing plug and play observer com.microchip.mplab.mdbcore.RI4Tool.RI4ToolBase$RI4PlugNPlayObserver@355daafb
3430 1731542539763 GEN4_CONNECT_DIAGNOSTICS:Begin PlugNPlayObservers list dump:
3430 1731542539763 GEN4_CONNECT_DIAGNOSTICS:End PlugNPlayObservers list dump:
3430 1731542539864 GEN4_CONNECT_DIAGNOSTICS:Calling RIDbgToolCom.Disconnect
3430 1731542539864 GEN4_CONNECT_DIAGNOSTICS:Calling MPLABCommTool.Detach to remove tool from plug and play list
3430 1731542539864 GEN4_CONNECT_DIAGNOSTICS:Calling RIDbgToolCom.DisconnectFromMPlabComm
3430 1731542539864 GEN4_CONNECT_DIAGNOSTICS:Calling MPLABCommTool.Disconnect
3442 1731542554224 GEN4_CONNECT_DIAGNOSTICS:MPLABCommTool is NOT null
3442 1731542554224 GEN4_CONNECT_DIAGNOSTICS:AttachedToolPID = 2175, AttachedToolVID = 3eb
3442 1731542554224 GEN4_CONNECT_DIAGNOSTICS:transport type = USB
3442 1731542554224 GEN4_CONNECT_DIAGNOSTICS:AttachedToolPID = 2175, AttachedToolVID = 3eb
3442 1731542554225 com.microchip.mplab.mdbcore.RealICETool.RIDbgToolCom
3442 1731542554225 GEN4_CONNECT_DIAGNOSTICS:Before MPLABCommTool.Connect()
3442 1731542554225 GEN4_CONNECT_DIAGNOSTICS:After MPLABCommTool.Connect()
3442 1731542554225 GEN4_CONNECT_DIAGNOSTICS:MPLABCommTool.Connect() returned MPLABCOMM_NO_ERROR
3442 1731542554225 GEN4_CONNECT_DIAGNOSTICS:Attaching to MPLABCommTool plugnplay
3442 1731542554225 GEN4_CONNECT_DIAGNOSTICS:Adding new plug and play observer com.microchip.mplab.mdbcore.RI4Tool.RI4ToolBase$RI4PlugNPlayObserver@3c89b81c
3442 1731542554225 GEN4_CONNECT_DIAGNOSTICS:Begin PlugNPlayObservers list dump:
3442 1731542554225 GEN4_CONNECT_DIAGNOSTICS:com.microchip.mplab.mdbcore.RI4Tool.RI4ToolBase$RI4PlugNPlayObserver@3c89b81c
3442 1731542554225 GEN4_CONNECT_DIAGNOSTICS:End PlugNPlayObservers list dump:
3442 1731542554225 GEN4_CONNECT_DIAGNOSTICS:Registering for alternate PNP notifications. CommPnPCriteria.cPIDList = [2172, 216F, 2173, 2174, 2fc0], CommPnPCriteria.cSerialNumber = mchp3314031800000963

3442 1731542554234 GEN4_TO_CONTROLLER_LOG:GEN4_INIT_INT_LOG_ATmega3208 Pre:init
3442 1731542554234 GEN4_TO_CONTROLLER_LOG:GEN4_INIT_INT_LOG_ATmega3208 Payload
3442 1731542554234 GEN4_TO_CONTROLLER_LOG:GEN4_INIT_INT_LOG_ATmega3208 DeviceInfo: Values:
3442 1731542554234 GEN4_TO_CONTROLLER_LOG:GEN4_INIT_INT_LOG_ATmega3208 DeviceInfo: pcAddress = 7fffffffffffffff, Vpp = 5,00, useRowEraseIfVoltageIsLow = false, voltageBelowWhichUseRowErase = 0,00, deviceName = ATmega3208, programmerType = 
3442 1731542554234 GEN4_TO_CONTROLLER_LOG:GEN4_INIT_INT_LOG_ATmega3208 DeviceInfo: MemInfo values:
3442 1731542554234 GEN4_TO_CONTROLLER_LOG:GEN4_INIT_INT_LOG_ATmega3208 DeviceInfo: mask = ffff, exists = true, startAddr = 00000000, endAddr = 00007fff, rowSize = 0080, rowEraseSize = 0080, addrInc = 0001, widthProgram = 0001
3442 1731542554234 GEN4_TO_CONTROLLER_LOG:GEN4_INIT_INT_LOG_ATmega3208 DeviceInfo: mask = 00ff, exists = true, startAddr = 00821280, endAddr = 0083128a, rowSize = 0001, rowEraseSize = 0000, addrInc = 0001, widthProgram = 0001
3442 1731542554234 GEN4_TO_CONTROLLER_LOG:GEN4_INIT_INT_LOG_ATmega3208 DeviceInfo: mask = 0000, exists = false, startAddr = 00000000, endAddr = 00000000, rowSize = 0000, rowEraseSize = 0000, addrInc = 0000, widthProgram = 0000
3442 1731542554234 GEN4_TO_CONTROLLER_LOG:GEN4_INIT_INT_LOG_ATmega3208 DeviceInfo: mask = 00ff, exists = true, startAddr = 00001400, endAddr = 000014ff, rowSize = 0040, rowEraseSize = 0000, addrInc = 0001, widthProgram = 0001
3442 1731542554234 GEN4_TO_CONTROLLER_LOG:GEN4_INIT_INT_LOG_ATmega3208 DeviceInfo: mask = 00ff, exists = true, startAddr = 00001300, endAddr = 0000133f, rowSize = 0040, rowEraseSize = 0000, addrInc = 0001, widthProgram = 0001
3442 1731542554234 GEN4_TO_CONTROLLER_LOG:GEN4_INIT_INT_LOG_ATmega3208 DeviceInfo: mask = 0000, exists = false, startAddr = 00000000, endAddr = 00000000, rowSize = 0000, rowEraseSize = 0080, addrInc = 0000, widthProgram = 0000
3442 1731542554234 GEN4_TO_CONTROLLER_LOG:GEN4_INIT_INT_LOG_ATmega3208 DeviceInfo: mask = 0000, exists = false, startAddr = 00000000, endAddr = 00000000, rowSize = 0000, rowEraseSize = 0000, addrInc = 0001, widthProgram = 0001
3442 1731542554234 GEN4_TO_CONTROLLER_LOG:GEN4_INIT_INT_LOG_ATmega3208 DeviceInfo: mask = 0000, exists = false, startAddr = 00000000, endAddr = 00000000, rowSize = 0000, rowEraseSize = 0000, addrInc = 0000, widthProgram = 0000
3442 1731542554234 GEN4_TO_CONTROLLER_LOG:GEN4_INIT_INT_LOG_ATmega3208 DeviceInfo: mask = 0000, exists = false, startAddr = 00000000, endAddr = 00000000, rowSize = 0000, rowEraseSize = 0000, addrInc = 0000, widthProgram = 0000
3442 1731542554234 GEN4_TO_CONTROLLER_LOG:GEN4_INIT_INT_LOG_ATmega3208 DeviceInfo: mask = 0000, exists = false, startAddr = 00000000, endAddr = 00000000, rowSize = 0000, rowEraseSize = 0000, addrInc = 0000, widthProgram = 0000
3442 1731542554234 GEN4_TO_CONTROLLER_LOG:GEN4_INIT_INT_LOG_ATmega3208 DeviceInfo: mask = 0000, exists = false, startAddr = 00000000, endAddr = 00000000, rowSize = 0000, rowEraseSize = 0000, addrInc = 0000, widthProgram = 0000
3442 1731542554234 GEN4_TO_CONTROLLER_LOG:GEN4_INIT_INT_LOG_ATmega3208 DeviceInfo: mask = 0000, exists = false, startAddr = 00000000, endAddr = 00000000, rowSize = 0000, rowEraseSize = 0000, addrInc = 0001, widthProgram = 0001
3442 1731542554234 GEN4_TO_CONTROLLER_LOG:GEN4_INIT_INT_LOG_ATmega3208 DeviceInfo: mask = 0000, exists = false, startAddr = 00000000, endAddr = 00000000, rowSize = 0000, rowEraseSize = 0000, addrInc = 0000, widthProgram = 0000
3442 1731542554234 GEN4_TO_CONTROLLER_LOG:GEN4_INIT_INT_LOG_ATmega3208 DeviceInfo: mask = 0000, exists = false, startAddr = 00000000, endAddr = 00000000, rowSize = 0000, rowEraseSize = 0000, addrInc = 0000, widthProgram = 0000
3442 1731542554234 GEN4_TO_CONTROLLER_LOG:GEN4_INIT_INT_LOG_ATmega3208 DeviceInfo: mask = 0000, exists = false, startAddr = 00000000, endAddr = 00000000, rowSize = 0000, rowEraseSize = 0000, addrInc = 0000, widthProgram = 0000
3442 1731542554234 GEN4_TO_CONTROLLER_LOG:GEN4_INIT_INT_LOG_ATmega3208 DeviceInfo: mask = 0000, exists = false, startAddr = 00000000, endAddr = 00000000, rowSize = 0000, rowEraseSize = 0000, addrInc = 0000, widthProgram = 0000
3442 1731542554234 GEN4_TO_CONTROLLER_LOG:GEN4_INIT_INT_LOG_ATmega3208 DeviceInfo: mask = 7fffffff, exists = true, startAddr = 00001100, endAddr = 0000117f, rowSize = 0001, rowEraseSize = 0000, addrInc = 0001, widthProgram = 0001
3442 1731542554234 GEN4_TO_CONTROLLER_LOG:GEN4_INIT_INT_LOG_ATmega3208 DeviceInfo: mask = 0000, exists = false, startAddr = 00000000, endAddr = 00000000, rowSize = 0000, rowEraseSize = 0000, addrInc = 0000, widthProgram = 0000
3442 1731542554234 GEN4_TO_CONTROLLER_LOG:GEN4_INIT_INT_LOG_ATmega3208 DeviceInfo: mask = 0000, exists = false, startAddr = 00000000, endAddr = 00000000, rowSize = 0000, rowEraseSize = 0000, addrInc = 0000, widthProgram = 0000
3442 1731542554234 GEN4_TO_CONTROLLER_LOG:GEN4_INIT_INT_LOG_ATmega3208 DeviceInfo: mask = 0000, exists = false, startAddr = 00000000, endAddr = 00000000, rowSize = 0000, rowEraseSize = 0000, addrInc = 0000, widthProgram = 0000
3442 1731542554234 GEN4_TO_CONTROLLER_LOG:GEN4_INIT_INT_LOG_ATmega3208 DeviceInfo: mask = 0000, exists = false, startAddr = 00000000, endAddr = 00000000, rowSize = 0000, rowEraseSize = 0000, addrInc = 0000, widthProgram = 0000
3442 1731542554234 GEN4_TO_CONTROLLER_LOG:GEN4_INIT_INT_LOG_ATmega3208 DeviceInfo: mask = 0000, exists = false, startAddr = 00000000, endAddr = 00000000, rowSize = 0000, rowEraseSize = 0000, addrInc = 0000, widthProgram = 0000
3442 1731542554234 GEN4_TO_CONTROLLER_LOG:GEN4_INIT_INT_LOG_ATmega3208 DeviceInfo: mask = 0000, exists = false, startAddr = 00000000, endAddr = 00000000, rowSize = 0000, rowEraseSize = 0000, addrInc = 0000, widthProgram = 0000
3442 1731542554234 GEN4_TO_CONTROLLER_LOG:GEN4_INIT_INT_LOG_ATmega3208 DeviceInfo: CfgRequiredBitsMask Values:
3442 1731542554234 GEN4_TO_CONTROLLER_LOG:GEN4_INIT_INT_LOG_ATmega3208 Address = 00001100, Mask = 00000000
3442 1731542554234 GEN4_TO_CONTROLLER_LOG:GEN4_INIT_INT_LOG_ATmega3208 Address = 00001101, Mask = 00000000
3442 1731542554234 GEN4_TO_CONTROLLER_LOG:GEN4_INIT_INT_LOG_ATmega3208 Address = 00001102, Mask = 00000000
3442 1731542554234 GEN4_TO_CONTROLLER_LOG:GEN4_INIT_INT_LOG_ATmega3208 Address = 00001103, Mask = 00000000
3442 1731542554234 GEN4_TO_CONTROLLER_LOG:GEN4_INIT_INT_LOG_ATmega3208 Address = 00001104, Mask = 00000000
3442 1731542554234 GEN4_TO_CONTROLLER_LOG:GEN4_INIT_INT_LOG_ATmega3208 Address = 00001105, Mask = 00000000
3442 1731542554234 GEN4_TO_CONTROLLER_LOG:GEN4_INIT_INT_LOG_ATmega3208 Address = 00001106, Mask = 00000000
3442 1731542554234 GEN4_TO_CONTROLLER_LOG:GEN4_INIT_INT_LOG_ATmega3208 Address = 00001107, Mask = 00000000
3442 1731542554234 GEN4_TO_CONTROLLER_LOG:GEN4_INIT_INT_LOG_ATmega3208 Address = 00001108, Mask = 00000000
3442 1731542554234 GEN4_TO_CONTROLLER_LOG:GEN4_INIT_INT_LOG_ATmega3208 Address = 00001109, Mask = 00000000
3442 1731542554234 GEN4_TO_CONTROLLER_LOG:GEN4_INIT_INT_LOG_ATmega3208 Address = 0000110a, Mask = 00000000
3442 1731542554234 GEN4_TO_CONTROLLER_LOG:GEN4_INIT_INT_LOG_ATmega3208 Address = 0000110b, Mask = 00000000
3442 1731542554234 GEN4_TO_CONTROLLER_LOG:GEN4_INIT_INT_LOG_ATmega3208 Address = 0000110c, Mask = 00000000
3442 1731542554234 GEN4_TO_CONTROLLER_LOG:GEN4_INIT_INT_LOG_ATmega3208 Address = 00001114, Mask = 00000000
3442 1731542554234 GEN4_TO_CONTROLLER_LOG:GEN4_INIT_INT_LOG_ATmega3208 Address = 00001118, Mask = 00000000
3442 1731542554234 GEN4_TO_CONTROLLER_LOG:GEN4_INIT_INT_LOG_ATmega3208 Address = 00001119, Mask = 00000000
3442 1731542554234 GEN4_TO_CONTROLLER_LOG:GEN4_INIT_INT_LOG_ATmega3208 Address = 0000111a, Mask = 00000000
3442 1731542554234 GEN4_TO_CONTROLLER_LOG:GEN4_INIT_INT_LOG_ATmega3208 Address = 0000111b, Mask = 00000000
3442 1731542554234 GEN4_TO_CONTROLLER_LOG:GEN4_INIT_INT_LOG_ATmega3208 Address = 00001120, Mask = 00000000
3442 1731542554234 GEN4_TO_CONTROLLER_LOG:GEN4_INIT_INT_LOG_ATmega3208 Address = 00001121, Mask = 00000000
3442 1731542554234 GEN4_TO_CONTROLLER_LOG:GEN4_INIT_INT_LOG_ATmega3208 Address = 00001122, Mask = 00000000
3442 1731542554234 GEN4_TO_CONTROLLER_LOG:GEN4_INIT_INT_LOG_ATmega3208 Address = 00001123, Mask = 00000000
3442 1731542554234 GEN4_TO_CONTROLLER_LOG:GEN4_INIT_INT_LOG_ATmega3208 Address = 00001124, Mask = 00000000
3442 1731542554234 GEN4_TO_CONTROLLER_LOG:GEN4_INIT_INT_LOG_ATmega3208 Address = 00001125, Mask = 00000000
3442 1731542554234 GEN4_TO_CONTROLLER_LOG:GEN4_INIT_INT_LOG_ATmega3208 Address = 0000112f, Mask = 00000000
3442 1731542554234 GEN4_TO_CONTROLLER_LOG:GEN4_INIT_INT_LOG_ATmega3208 Address = 00821280, Mask = 000000ff
3442 1731542554234 GEN4_TO_CONTROLLER_LOG:GEN4_INIT_INT_LOG_ATmega3208 Address = 00821281, Mask = 000000ff
3442 1731542554234 GEN4_TO_CONTROLLER_LOG:GEN4_INIT_INT_LOG_ATmega3208 Address = 00821282, Mask = 00000083
3442 1731542554234 GEN4_TO_CONTROLLER_LOG:GEN4_INIT_INT_LOG_ATmega3208 Address = 00821285, Mask = 000000c9
3442 1731542554234 GEN4_TO_CONTROLLER_LOG:GEN4_INIT_INT_LOG_ATmega3208 Address = 00821286, Mask = 00000007
3442 1731542554234 GEN4_TO_CONTROLLER_LOG:GEN4_INIT_INT_LOG_ATmega3208 Address = 00821287, Mask = 000000ff
3442 1731542554234 GEN4_TO_CONTROLLER_LOG:GEN4_INIT_INT_LOG_ATmega3208 Address = 00821288, Mask = 000000ff
3442 1731542554234 GEN4_TO_CONTROLLER_LOG:GEN4_INIT_INT_LOG_ATmega3208 Address = 0083128a, Mask = 000000ff
3442 1731542554234 GEN4_TO_CONTROLLER_LOG:GEN4_INIT_INT_LOG_ATmega3208 BasicInfo: Values:
3442 1731542554234 GEN4_TO_CONTROLLER_LOG:GEN4_INIT_INT_LOG_ATmega3208 Payload End
3442 1731542554234 GEN4_TO_CONTROLLER_LOG:GEN4_INIT_INT_LOG_ATmega3208 Post:init
3442 1731542554234 GEN4_TO_CONTROLLER_LOG:GEN4_INIT_INT_LOG_ATmega3208 Return Value
3442 1731542554234 GEN4_TO_CONTROLLER_LOG:GEN4_INIT_INT_LOG_ATmega3208 none
3442 1731542554234 GEN4_TO_CONTROLLER_LOG:GEN4_INIT_INT_LOG_ATmega3208 Return End

3442 1731542554234 GEN4_TO_CONTROLLER_LOG:GEN4_INIT_INT_LOG_ATmega3208 Pre:GetInterfaceProvider
3442 1731542554234 GEN4_TO_CONTROLLER_LOG:GEN4_INIT_INT_LOG_ATmega3208 Payload
3442 1731542554234 GEN4_TO_CONTROLLER_LOG:GEN4_INIT_INT_LOG_ATmega3208 RI4DebugInterface
3442 1731542554234 GEN4_TO_CONTROLLER_LOG:GEN4_INIT_INT_LOG_ATmega3208 Payload End
3442 1731542554234 GEN4_TO_CONTROLLER_LOG:GEN4_INIT_INT_LOG_ATmega3208 Post:GetInterfaceProvider
3442 1731542554234 GEN4_TO_CONTROLLER_LOG:GEN4_INIT_INT_LOG_ATmega3208 Return Value
3442 1731542554234 GEN4_TO_CONTROLLER_LOG:GEN4_INIT_INT_LOG_ATmega3208 com.microchip.mplab.libs.atmelice.implementations.DebugInterface@49ffe85f
3442 1731542554234 GEN4_TO_CONTROLLER_LOG:GEN4_INIT_INT_LOG_ATmega3208 Return End

3442 1731542554235 GEN4_TO_CONTROLLER_LOG:GEN4_INIT_INT_LOG_ATmega3208 Pre:GetInterfaceProvider
3442 1731542554235 GEN4_TO_CONTROLLER_LOG:GEN4_INIT_INT_LOG_ATmega3208 Payload
3442 1731542554235 GEN4_TO_CONTROLLER_LOG:GEN4_INIT_INT_LOG_ATmega3208 RI4ProgramInterface
3442 1731542554235 GEN4_TO_CONTROLLER_LOG:GEN4_INIT_INT_LOG_ATmega3208 Payload End
3442 1731542554235 GEN4_TO_CONTROLLER_LOG:GEN4_INIT_INT_LOG_ATmega3208 Post:GetInterfaceProvider
3442 1731542554235 GEN4_TO_CONTROLLER_LOG:GEN4_INIT_INT_LOG_ATmega3208 Return Value
3442 1731542554235 GEN4_TO_CONTROLLER_LOG:GEN4_INIT_INT_LOG_ATmega3208 com.microchip.mplab.libs.atmelice.implementations.ProgramInterface@38c7e024
3442 1731542554235 GEN4_TO_CONTROLLER_LOG:GEN4_INIT_INT_LOG_ATmega3208 Return End

3442 1731542554235 GEN4_TO_CONTROLLER_LOG:GEN4_INIT_INT_LOG_ATmega3208 Pre:GetInterfaceProvider
3442 1731542554235 GEN4_TO_CONTROLLER_LOG:GEN4_INIT_INT_LOG_ATmega3208 Payload
3442 1731542554235 GEN4_TO_CONTROLLER_LOG:GEN4_INIT_INT_LOG_ATmega3208 RI4ConnectInterface
3442 1731542554235 GEN4_TO_CONTROLLER_LOG:GEN4_INIT_INT_LOG_ATmega3208 Payload End
3442 1731542554235 GEN4_TO_CONTROLLER_LOG:GEN4_INIT_INT_LOG_ATmega3208 Post:GetInterfaceProvider
3442 1731542554235 GEN4_TO_CONTROLLER_LOG:GEN4_INIT_INT_LOG_ATmega3208 Return Value
3442 1731542554235 GEN4_TO_CONTROLLER_LOG:GEN4_INIT_INT_LOG_ATmega3208 com.microchip.mplab.libs.atmelice.implementations.ConnectInterface@78b87ed0
3442 1731542554235 GEN4_TO_CONTROLLER_LOG:GEN4_INIT_INT_LOG_ATmega3208 Return End

3442 1731542554235 GEN4_TO_CONTROLLER_LOG:GEN4_INIT_INT_LOG_ATmega3208 Pre:GetInterfaceProvider
3442 1731542554235 GEN4_TO_CONTROLLER_LOG:GEN4_INIT_INT_LOG_ATmega3208 Payload
3442 1731542554235 GEN4_TO_CONTROLLER_LOG:GEN4_INIT_INT_LOG_ATmega3208 RI4ControllerDiagnosticsInterface
3442 1731542554235 GEN4_TO_CONTROLLER_LOG:GEN4_INIT_INT_LOG_ATmega3208 Payload End
3442 1731542554235 GEN4_TO_CONTROLLER_LOG:GEN4_INIT_INT_LOG_ATmega3208 Post:GetInterfaceProvider
3442 1731542554235 GEN4_TO_CONTROLLER_LOG:GEN4_INIT_INT_LOG_ATmega3208 Return Value
3442 1731542554235 GEN4_TO_CONTROLLER_LOG:GEN4_INIT_INT_LOG_ATmega3208 com.microchip.mplab.libs.atmelice.implementations.UnimplementedDiagnostics@a3569a
3442 1731542554235 GEN4_TO_CONTROLLER_LOG:GEN4_INIT_INT_LOG_ATmega3208 Return End

3442 1731542554235 GEN4_TO_CONTROLLER_LOG:GEN4_INIT_INT_LOG_ATmega3208 Pre:GetInterfaceProvider
3442 1731542554235 GEN4_TO_CONTROLLER_LOG:GEN4_INIT_INT_LOG_ATmega3208 Payload
3442 1731542554235 GEN4_TO_CONTROLLER_LOG:GEN4_INIT_INT_LOG_ATmega3208 ProgrammerToGo
3442 1731542554235 GEN4_TO_CONTROLLER_LOG:GEN4_INIT_INT_LOG_ATmega3208 Payload End
3442 1731542554235 GEN4_TO_CONTROLLER_LOG:GEN4_INIT_INT_LOG_ATmega3208 Post:GetInterfaceProvider
3442 1731542554235 GEN4_TO_CONTROLLER_LOG:GEN4_INIT_INT_LOG_ATmega3208 Return Value
3442 1731542554235 GEN4_TO_CONTROLLER_LOG:GEN4_INIT_INT_LOG_ATmega3208 null
3442 1731542554235 GEN4_TO_CONTROLLER_LOG:GEN4_INIT_INT_LOG_ATmega3208 Return End

3442 1731542554235 GEN4_TO_CONTROLLER_LOG:GEN4_INIT_INT_LOG_ATmega3208 Pre:GetInterfaceProvider
3442 1731542554235 GEN4_TO_CONTROLLER_LOG:GEN4_INIT_INT_LOG_ATmega3208 Payload
3442 1731542554235 GEN4_TO_CONTROLLER_LOG:GEN4_INIT_INT_LOG_ATmega3208 Status
3442 1731542554235 GEN4_TO_CONTROLLER_LOG:GEN4_INIT_INT_LOG_ATmega3208 Payload End
3442 1731542554235 GEN4_TO_CONTROLLER_LOG:GEN4_INIT_INT_LOG_ATmega3208 Post:GetInterfaceProvider
3442 1731542554235 GEN4_TO_CONTROLLER_LOG:GEN4_INIT_INT_LOG_ATmega3208 Return Value
3442 1731542554235 GEN4_TO_CONTROLLER_LOG:GEN4_INIT_INT_LOG_ATmega3208 null
3442 1731542554235 GEN4_TO_CONTROLLER_LOG:GEN4_INIT_INT_LOG_ATmega3208 Return End

3442 1731542554237 GEN4_TO_CONTROLLER_LOG:GEN4_CONNECT_INT_LOG Pre:EstablishCommunincations
3442 1731542554237 GEN4_TO_CONTROLLER_LOG:GEN4_CONNECT_INT_LOG Payload
3442 1731542554237 GEN4_TO_CONTROLLER_LOG:GEN4_CONNECT_INT_LOG com.microchip.mplab.mdbcore.AtmelIceScripting.AIceScriptingCom@3628fbc1
3442 1731542554237 GEN4_TO_CONTROLLER_LOG:GEN4_CONNECT_INT_LOG Payload End
3442 1731542554237 NativeController::EstablishCommunincations entry
3442 1731542554237 pro JtagIce3 [0x00] <<< 00 00 00 
3442 1731542554243 pro JtagIce3 [0x00] >>> 81 00 00 01 12 20 
3442 1731542554243 pro JtagIce3 [0x01] <<< 10 00 
3442 1731542554247 pro JtagIce3 [0x01] >>> 80 00 
3442 1731542554247 pro JtagIce3 [0x00] <<< 00 00 03 
3442 1731542554251 pro JtagIce3 [0x00] >>> 81 00 08 
3442 1731542554251 NativeController::EstablishCommunincations exit
3442 1731542554251 GEN4_TO_CONTROLLER_LOG:GEN4_CONNECT_INT_LOG Post:EstablishCommunincations
3442 1731542554251 GEN4_TO_CONTROLLER_LOG:GEN4_CONNECT_INT_LOG Return Value
3442 1731542554251 GEN4_TO_CONTROLLER_LOG:GEN4_CONNECT_INT_LOG true
3442 1731542554251 GEN4_TO_CONTROLLER_LOG:GEN4_CONNECT_INT_LOG Return End

3442 1731542554251 GEN4_TO_CONTROLLER_LOG:GEN4_CONNECT_INT_LOG Pre:GetFirmwareInfo
3442 1731542554251 GEN4_TO_CONTROLLER_LOG:GEN4_CONNECT_INT_LOG Payload
3442 1731542554251 GEN4_TO_CONTROLLER_LOG:GEN4_CONNECT_INT_LOG null
3442 1731542554251 GEN4_TO_CONTROLLER_LOG:GEN4_CONNECT_INT_LOG Payload End
3442 1731542554251 NativeController::GetFirmwareInfo entry
3442 1731542554251 pro JtagIce3 [0x01] <<< 02 00 00 00 01 
3442 1731542554255 pro JtagIce3 [0x01] >>> 84 01 00 00 
3442 1731542554255 NativeController::getFirmwareVersion entry
3442 1731542554255 pro JtagIce3 [0x01] <<< 02 00 00 01 01 
3442 1731542554259 pro JtagIce3 [0x01] >>> 84 01 01 00 
3442 1731542554259 pro JtagIce3 [0x01] <<< 02 00 00 02 01 
3442 1731542554263 pro JtagIce3 [0x01] >>> 84 01 1E 00 
3442 1731542554263 pro JtagIce3 [0x01] <<< 02 00 00 03 02 
3442 1731542554267 pro JtagIce3 [0x01] >>> 84 01 23 00 00 
3442 1731542554267 NativeController::getFirmwareVersion exit
3442 1731542554267 pro JtagIce3 [0x01] <<< 02 00 00 09 01 
3442 1731542554271 pro JtagIce3 [0x01] >>> 84 01 00 11 
3442 1731542554271 NativeController::tryGetFPGAVersion entry
3442 1731542554271 pro JtagIce3 [0x01] <<< 02 00 00 10 01 
3442 1731542554275 pro JtagIce3 [0x01] >>> 84 01 00 11 
3442 1731542554275 pro JtagIce3 [0x01] <<< 02 00 00 11 01 
3442 1731542554279 pro JtagIce3 [0x01] >>> 84 01 00 11 
3442 1731542554279 pro JtagIce3 [0x01] <<< 02 00 00 12 01 
3442 1731542554283 pro JtagIce3 [0x01] >>> 84 01 00 11 
3442 1731542554283 NativeController::tryGetFPGAVersion exit
3442 1731542554283 NativeController::tryGetFPGAVersion exit with exception No value present
3442 1731542554283 pro JtagIce3 [0x01] <<< 02 00 00 06 01 
3442 1731542554287 pro JtagIce3 [0x01] >>> 84 01 00 00 
3442 1731542554287 pro JtagIce3 [0x01] <<< 02 00 00 07 01 
3442 1731542554291 pro JtagIce3 [0x01] >>> 84 01 00 00 
3442 1731542554291 pro JtagIce3 [0x01] <<< 02 00 00 0A 01 
3442 1731542554295 pro JtagIce3 [0x01] >>> 84 01 00 00 
3442 1731542554295 NativeController::GetFirmwareInfo exit
3442 1731542554295 GEN4_TO_CONTROLLER_LOG:GEN4_CONNECT_INT_LOG Post:GetFirmwareInfo
3442 1731542554295 GEN4_TO_CONTROLLER_LOG:GEN4_CONNECT_INT_LOG Return Value
3442 1731542554295 GEN4_TO_CONTROLLER_LOG:GEN4_CONNECT_INT_LOG FirmwareInfo: Values:
3442 1731542554295 GEN4_TO_CONTROLLER_LOG:GEN4_CONNECT_INT_LOG FirmwareInfo: boot = false, bootVer = 0.0.0 (0x00.0x00.0x00), apVer = 1.30.35 (0x01.0x1e.0x23), fpgaVer = null, scriptVer = null, macAddress = , devID = 0, devID1 = 0, devSN0 = 0, devSN1 = 0, serialNumber = null, appCommitID = null, scriptCommitID = null, PCB_ID = 0
3442 1731542554295 GEN4_TO_CONTROLLER_LOG:GEN4_CONNECT_INT_LOG Return End
3442 1731542554295 GEN4_CONNECT_DIAGNOSTICS:ENTERING: com.microchip.mplab.mdbcore.RI4Tool.ConnectionHandler.CheckForFWUpdates()
3442 1731542554295 GEN4_CONNECT_DIAGNOSTICS:Created FirmwareUpdateHandler com.microchip.mplab.mdbcore.AtmelIceScripting.OperationHandlers.AIceScriptingFirmwareUpdateHandler@3169fbe0

3442 1731542554299 GEN4_TO_CONTROLLER_LOG:GEN4_CONNECT_INT_LOG Pre:SetUpdateFirmwareInfo
3442 1731542554299 GEN4_TO_CONTROLLER_LOG:GEN4_CONNECT_INT_LOG Payload
3442 1731542554299 GEN4_TO_CONTROLLER_LOG:GEN4_CONNECT_INT_LOG UpdateFirmwareInfo: Values:
3442 1731542554299 GEN4_TO_CONTROLLER_LOG:GEN4_CONNECT_INT_LOG UpdateFirmwareInfo: license = , updateId = 0
3442 1731542554299 GEN4_TO_CONTROLLER_LOG:GEN4_CONNECT_INT_LOG Payload End
3442 1731542554299 GEN4_TO_CONTROLLER_LOG:GEN4_CONNECT_INT_LOG Post:SetUpdateFirmwareInfo
3442 1731542554299 GEN4_TO_CONTROLLER_LOG:GEN4_CONNECT_INT_LOG Return Value
3442 1731542554299 GEN4_TO_CONTROLLER_LOG:GEN4_CONNECT_INT_LOG none
3442 1731542554299 GEN4_TO_CONTROLLER_LOG:GEN4_CONNECT_INT_LOG Return End
3442 1731542554299 GEN4_CONNECT_DIAGNOSTICS:EXITING: com.microchip.mplab.mdbcore.RI4Tool.ConnectionHandler.CheckForFWUpdates()

3442 1731542554299 GEN4_TO_CONTROLLER_LOG:GEN4_CONNECT_INT_LOG Pre:SetPowerInfo
3442 1731542554299 GEN4_TO_CONTROLLER_LOG:GEN4_CONNECT_INT_LOG Payload
3442 1731542554299 GEN4_TO_CONTROLLER_LOG:GEN4_CONNECT_INT_LOG PowerInfo: Values:
3442 1731542554299 GEN4_TO_CONTROLLER_LOG:GEN4_CONNECT_INT_LOG PowerInfo: shotDownSystem = false, isToolPower = false, voltage = 5,000000, useVppFirst = false, useLowVoltageProgramming = true, useMaintainActivePower = false
3442 1731542554299 GEN4_TO_CONTROLLER_LOG:GEN4_CONNECT_INT_LOG Payload End
3442 1731542554299 NativeController::GetVoltageInfo entry
3442 1731542554299 pro JtagIce3 [0x01] <<< 02 00 01 00 02 
3442 1731542554303 pro JtagIce3 [0x01] >>> 84 01 E2 0C 00 
3442 1731542554303 pro JtagIce3 [0x01] <<< 02 00 01 20 02 
3442 1731542554307 pro JtagIce3 [0x01] >>> 84 01 E4 0C 00 
3442 1731542554307 pro JtagIce3 [0x01] <<< 02 00 01 02 02 
3442 1731542554311 pro JtagIce3 [0x01] >>> 84 01 0C 00 00 
3442 1731542554311 NativeController::GetVoltageInfo exit
3442 1731542554311 GEN4_TO_CONTROLLER_LOG:GEN4_CONNECT_INT_LOG Post:SetPowerInfo
3442 1731542554311 GEN4_TO_CONTROLLER_LOG:GEN4_CONNECT_INT_LOG Return Value
3442 1731542554311 GEN4_TO_CONTROLLER_LOG:GEN4_CONNECT_INT_LOG none
3442 1731542554311 GEN4_TO_CONTROLLER_LOG:GEN4_CONNECT_INT_LOG Return End

3442 1731542554311 GEN4_TO_CONTROLLER_LOG:GEN4_CONNECT_INT_LOG Pre:GetVoltageInfo
3442 1731542554311 GEN4_TO_CONTROLLER_LOG:GEN4_CONNECT_INT_LOG Payload
3442 1731542554311 GEN4_TO_CONTROLLER_LOG:GEN4_CONNECT_INT_LOG null
3442 1731542554311 GEN4_TO_CONTROLLER_LOG:GEN4_CONNECT_INT_LOG Payload End
3442 1731542554311 NativeController::GetVoltageInfo entry
3442 1731542554311 pro JtagIce3 [0x01] <<< 02 00 01 00 02 
3442 1731542554315 pro JtagIce3 [0x01] >>> 84 01 E2 0C 00 
3442 1731542554315 pro JtagIce3 [0x01] <<< 02 00 01 20 02 
3442 1731542554319 pro JtagIce3 [0x01] >>> 84 01 E4 0C 00 
3442 1731542554319 pro JtagIce3 [0x01] <<< 02 00 01 02 02 
3442 1731542554323 pro JtagIce3 [0x01] >>> 84 01 0C 00 00 
3442 1731542554323 NativeController::GetVoltageInfo exit
3442 1731542554323 GEN4_TO_CONTROLLER_LOG:GEN4_CONNECT_INT_LOG Post:GetVoltageInfo
3442 1731542554323 GEN4_TO_CONTROLLER_LOG:GEN4_CONNECT_INT_LOG Return Value
3442 1731542554323 GEN4_TO_CONTROLLER_LOG:GEN4_CONNECT_INT_LOG VoltagesInfo: Values:
3442 1731542554323 GEN4_TO_CONTROLLER_LOG:GEN4_CONNECT_INT_LOG VoltagesInfo: internalVdd = 0, internalVpp = 0, targetVdd = 0, targetVpp = 3300, vddSense = 3298, temp = 0, vddCurrentSense = 0, vddVoltageSense = 12
3442 1731542554323 GEN4_TO_CONTROLLER_LOG:GEN4_CONNECT_INT_LOG Return End

3442 1731542554323 GEN4_TO_CONTROLLER_LOG:GEN4_CONNECT_INT_LOG Pre:SetLEDBrightness
3442 1731542554323 GEN4_TO_CONTROLLER_LOG:GEN4_CONNECT_INT_LOG Payload
3442 1731542554323 GEN4_TO_CONTROLLER_LOG:GEN4_CONNECT_INT_LOG 5
3442 1731542554323 GEN4_TO_CONTROLLER_LOG:GEN4_CONNECT_INT_LOG Payload End
3442 1731542554323 GEN4_TO_CONTROLLER_LOG:GEN4_CONNECT_INT_LOG Post:SetLEDBrightness
3442 1731542554323 GEN4_TO_CONTROLLER_LOG:GEN4_CONNECT_INT_LOG Return Value
3442 1731542554323 GEN4_TO_CONTROLLER_LOG:GEN4_CONNECT_INT_LOG none
3442 1731542554323 GEN4_TO_CONTROLLER_LOG:GEN4_CONNECT_INT_LOG Return End

3442 1731542554323 GEN4_TO_CONTROLLER_LOG:GEN4_CONNECT_INT_LOG Pre:SetToolInfo
3442 1731542554323 GEN4_TO_CONTROLLER_LOG:GEN4_CONNECT_INT_LOG Payload
3442 1731542554323 GEN4_TO_CONTROLLER_LOG:GEN4_CONNECT_INT_LOG ToolInfo: Values:
3442 1731542554323 GEN4_TO_CONTROLLER_LOG:GEN4_CONNECT_INT_LOG ToolInfo: speedLevel = 1, PGCResistance = 4700, PGDResistance = 4700, PGCPullDir = PullDown, PGDPullDir = PullDown, ICSPSelected = Wire2
3442 1731542554323 GEN4_TO_CONTROLLER_LOG:GEN4_CONNECT_INT_LOG Payload End
3442 1731542554323 GEN4_TO_CONTROLLER_LOG:GEN4_CONNECT_INT_LOG Post:SetToolInfo
3442 1731542554323 GEN4_TO_CONTROLLER_LOG:GEN4_CONNECT_INT_LOG Return Value
3442 1731542554323 GEN4_TO_CONTROLLER_LOG:GEN4_CONNECT_INT_LOG none
3442 1731542554323 GEN4_TO_CONTROLLER_LOG:GEN4_CONNECT_INT_LOG Return End

3442 1731542554324 GEN4_TO_CONTROLLER_LOG:GEN4_CONNECT_INT_LOG Pre:GetTargetIDInfo
3442 1731542554324 GEN4_TO_CONTROLLER_LOG:GEN4_CONNECT_INT_LOG Payload
3442 1731542554324 GEN4_TO_CONTROLLER_LOG:GEN4_CONNECT_INT_LOG null
3442 1731542554324 GEN4_TO_CONTROLLER_LOG:GEN4_CONNECT_INT_LOG Payload End
3442 1731542554324 NativeController::GetTargetIDInfo entry
3442 1731542554324 pro JtagIce3 [0x12] <<< 01 00 01 31 02 F4 01 
3442 1731542554328 pro JtagIce3 [0x12] >>> 80 00 
3442 1731542554328 pro JtagIce3 [0x12] <<< 01 00 00 00 01 05 
3442 1731542554332 pro JtagIce3 [0x12] >>> 80 00 
3442 1731542554332 pro JtagIce3 [0x12] <<< 01 00 00 01 01 01 
3442 1731542554336 pro JtagIce3 [0x12] >>> 80 00 
3442 1731542554336 pro JtagIce3 [0x12] <<< 01 00 01 00 01 08 
3442 1731542554340 pro JtagIce3 [0x12] >>> 80 00 
3442 1731542554340 pro JtagIce3 [0x12] <<< 01 00 02 00 30 00 40 80 40 00 10 80 0F 94 11 8C 0A 98 08 DC 05 DC 05 00 80 00 00 00 01 40 00 0A 05 FF 00 FF 00 00 14 00 13 00 11 80 12 8A 12 30 95 00 00 00 01 
3442 1731542554344 pro JtagIce3 [0x12] >>> 80 00 
3442 1731542554344 pro JtagIce3 [0x12] <<< 01 00 03 06 01 00 
3442 1731542554348 pro JtagIce3 [0x12] >>> 80 00 
3442 1731542554348 pro JtagIce3 [0x12] <<< 10 00 00 
3442 1731542554369 pro JtagIce3 [0x12] >>> 84 00 6D 65 67 61 00 
3442 1731542554369 pro JtagIce3 [0x12] <<< 01 00 03 06 01 00 
3442 1731542554373 pro JtagIce3 [0x12] >>> 80 00 
3442 1731542554373 pro JtagIce3 [0x12] <<< 15 00 
3442 1731542554440 pro JtagIce3 [0x12] >>> 80 00 
3442 1731542554440 pro JtagIce3 [0x12] <<< 21 00 B4 00 11 00 00 03 00 00 00 
3442 1731542554444 pro JtagIce3 [0x12] >>> 84 00 1E 95 30 00 
3442 1731542554444 pro JtagIce3 [0x12] <<< 21 00 B4 00 11 00 00 03 00 00 00 
3442 1731542554448 pro JtagIce3 [0x12] >>> 84 00 1E 95 30 00 
3442 1731542554448 pro JtagIce3 [0x12] <<< 21 00 B4 00 11 00 00 03 00 00 00 
3442 1731542554452 pro JtagIce3 [0x12] >>> 84 00 1E 95 30 00 
3442 1731542554452 pro JtagIce3 [0x12] <<< 21 00 B2 01 0F 00 00 01 00 00 00 
3442 1731542554456 pro JtagIce3 [0x12] >>> 84 00 01 00 
3442 1731542554456 pro JtagIce3 [0x12] <<< 16 00 
3442 1731542554460 pro JtagIce3 [0x12] >>> 80 00 
3442 1731542554460 pro JtagIce3 [0x12] <<< 11 00 
3442 1731542554464 pro JtagIce3 [0x12] >>> 80 00 
3442 1731542554464 pro JtagIce3 [0x01] <<< 11 00 00 
3442 1731542554468 pro JtagIce3 [0x01] >>> 80 00 
3442 1731542554468 NativeController::GetTargetIDInfo exit device ID 0x1e9530
3442 1731542554468 GEN4_TO_CONTROLLER_LOG:GEN4_CONNECT_INT_LOG Post:GetTargetIDInfo
3442 1731542554468 GEN4_TO_CONTROLLER_LOG:GEN4_CONNECT_INT_LOG Return Value
3442 1731542554468 GEN4_TO_CONTROLLER_LOG:GEN4_CONNECT_INT_LOG TargetIDInfo: Values:
3442 1731542554468 GEN4_TO_CONTROLLER_LOG:GEN4_CONNECT_INT_LOG TargetIDInfo: DeviceID = 001e9530
3442 1731542554468 GEN4_TO_CONTROLLER_LOG:GEN4_CONNECT_INT_LOG Return End

3442 1731542554471 GEN4_TO_CONTROLLER_LOG:GEN4_PROGRAM_INT_LOG_ATmega3208 Pre:SendOperation
3442 1731542554471 GEN4_TO_CONTROLLER_LOG:GEN4_PROGRAM_INT_LOG_ATmega3208 Payload
3442 1731542554471 GEN4_TO_CONTROLLER_LOG:GEN4_PROGRAM_INT_LOG_ATmega3208 OperationInfo: Values:
3442 1731542554471 GEN4_TO_CONTROLLER_LOG:GEN4_PROGRAM_INT_LOG_ATmega3208 OperationInfo: Type = erase, Mask = 00000000, Erase = false, Production Mode = true
3442 1731542554471 GEN4_TO_CONTROLLER_LOG:GEN4_PROGRAM_INT_LOG_ATmega3208 TransferInfo: Start = 0, End = 7fff, Buffer Length = 0, Type = Pgm, Mask = 00000000
3442 1731542554471 GEN4_TO_CONTROLLER_LOG:GEN4_PROGRAM_INT_LOG_ATmega3208 TransferInfo: Start = 1280, End = 1288, Buffer Length = 0, Type = Cfg, Mask = 00000000
3442 1731542554471 GEN4_TO_CONTROLLER_LOG:GEN4_PROGRAM_INT_LOG_ATmega3208 TransferInfo: Start = 128a, End = 128a, Buffer Length = 0, Type = Cfg, Mask = 00000000
3442 1731542554471 GEN4_TO_CONTROLLER_LOG:GEN4_PROGRAM_INT_LOG_ATmega3208 TransferInfo: Start = 1400, End = 14ff, Buffer Length = 0, Type = EEData, Mask = 00000000
3442 1731542554471 GEN4_TO_CONTROLLER_LOG:GEN4_PROGRAM_INT_LOG_ATmega3208 TransferInfo: Start = 1300, End = 133f, Buffer Length = 0, Type = UserID, Mask = 00000000
3442 1731542554471 GEN4_TO_CONTROLLER_LOG:GEN4_PROGRAM_INT_LOG_ATmega3208 Payload End
3442 1731542554471 pro JtagIce3 [0x12] <<< 01 00 01 31 02 F4 01 
3442 1731542554475 pro JtagIce3 [0x12] >>> 80 00 
3442 1731542554475 pro JtagIce3 [0x12] <<< 01 00 00 00 01 05 
3442 1731542554479 pro JtagIce3 [0x12] >>> 80 00 
3442 1731542554479 pro JtagIce3 [0x12] <<< 01 00 00 01 01 01 
3442 1731542554483 pro JtagIce3 [0x12] >>> 80 00 
3442 1731542554483 pro JtagIce3 [0x12] <<< 01 00 01 00 01 08 
3442 1731542554487 pro JtagIce3 [0x12] >>> 80 00 
3442 1731542554487 pro JtagIce3 [0x12] <<< 01 00 02 00 30 00 40 80 40 00 10 80 0F 94 11 8C 0A 98 08 DC 05 DC 05 00 80 00 00 00 01 40 00 0A 05 FF 00 FF 00 00 14 00 13 00 11 80 12 8A 12 30 95 00 00 00 01 
3442 1731542554491 pro JtagIce3 [0x12] >>> 80 00 
3442 1731542554491 pro JtagIce3 [0x12] <<< 01 00 03 06 01 00 
3442 1731542554495 pro JtagIce3 [0x12] >>> 80 00 
3442 1731542554495 pro JtagIce3 [0x12] <<< 10 00 00 
3442 1731542554516 pro JtagIce3 [0x12] >>> 84 00 6D 65 67 61 00 
3442 1731542554516 pro JtagIce3 [0x12] <<< 01 00 03 06 01 00 
3442 1731542554520 pro JtagIce3 [0x12] >>> 80 00 
3442 1731542554520 pro JtagIce3 [0x12] <<< 15 00 
3442 1731542554587 pro JtagIce3 [0x12] >>> 80 00 
3442 1731542554587 pro JtagIce3 [0x12] <<< 21 00 B4 00 11 00 00 03 00 00 00 
3442 1731542554591 pro JtagIce3 [0x12] >>> 84 00 1E 95 30 00 
3442 1731542554591 pro JtagIce3 [0x12] <<< 20 00 00 00 00 00 00 
3442 1731542554598 pro JtagIce3 [0x12] >>> 80 00 
3442 1731542554598 pro JtagIce3 [0x12] <<< 21 00 B2 85 12 00 00 01 00 00 00 
3442 1731542554602 pro JtagIce3 [0x12] >>> 84 00 C0 00 
3442 1731542554602 pro JtagIce3 [0x12] <<< 23 00 B2 85 12 00 00 01 00 00 00 00 C0 
3442 1731542554610 pro JtagIce3 [0x12] >>> 80 00 
3442 1731542554610 pro JtagIce3 [0x12] <<< 21 00 B2 85 12 00 00 01 00 00 00 
3442 1731542554614 pro JtagIce3 [0x12] >>> 84 00 C0 00 
3442 1731542554614 pro JtagIce3 [0x12] <<< 23 00 B2 85 12 00 00 01 00 00 00 00 C0 
3442 1731542554622 pro JtagIce3 [0x12] >>> 80 00 
3442 1731542554622 pro JtagIce3 [0x12] <<< 20 00 00 00 00 00 00 
3442 1731542554629 pro JtagIce3 [0x12] >>> 80 00 
3442 1731542554629 GEN4_TO_CONTROLLER_LOG:GEN4_PROGRAM_INT_LOG_ATmega3208 Post:SendOperation
3442 1731542554629 GEN4_TO_CONTROLLER_LOG:GEN4_PROGRAM_INT_LOG_ATmega3208 Return Value
3442 1731542554629 GEN4_TO_CONTROLLER_LOG:GEN4_PROGRAM_INT_LOG_ATmega3208 None
3442 1731542554629 GEN4_TO_CONTROLLER_LOG:GEN4_PROGRAM_INT_LOG_ATmega3208 Return End
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

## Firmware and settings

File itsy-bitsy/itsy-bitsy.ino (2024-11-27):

// Arduino9x_RX
// -*- mode: C++ -*-
// Example sketch showing how to create a simple messaging client (receiver)
// with the RH_RF95 class. RH_RF95 class does not provide for addressing or
// reliability, so you should only use RH_RF95 if you do not need the higher
// level messaging abilities.
// It is designed to work with the other example Arduino9x_TX
// workspace link: https://adafruit.github.io/arduino-board-index/package_adafruit_index.json
// also uses RadioHead library, and the code is modified from: https://github.com/adafruit/RadioHead/blob/master/examples/feather/Feather9x_RX/Feather9x_RX.ino

/*
Radio datasheets:
https://cdn-learn.adafruit.com/downloads/pdf/adafruit-rfm69hcw-and-rfm96-rfm95-rfm98-lora-packet-padio-breakouts.pdf
https://cdn-shop.adafruit.com/product-files/3076/sx1231.pdf
*/

/*
itsy-bitsy pinouts:
https://learn.adafruit.com/introducting-itsy-bitsy-32u4/pinouts
*/

#include <SPI.h>
#include <RH_RF95.h>

/* Chip Select pin - A0, PF7 */
#define RFM95_CS_PIN         18
/* Reset pin - A1, PF6 */
#define RFM95_RST_PIN        19
/* G0 interrupt pin - PD0 */
#define RFM95_INT_PIN        0
/* lora LED indicator - PB7 */
#define LORA_LED_PIN         11

/* ADC - A2, PF5, ADC5 */
#define ADC_PIN              20
/* threshold ADC output to consider power on */
#define ADC_THRESH           100

/* continuity green and red channels - PD6, PC7 */
#define GREEN_CONT_LED_PIN   12
#define RED_CONT_LED_PIN     13

/* Relay pin - PD3 */
#define RELAY_PIN            1

/* Change to 433.0 or other frequency, must match RX's freq! */
#define RF95_FREQ 433.0

/* Singleton instance of the radio driver */
RH_RF95 lora(RFM95_CS_PIN, RFM95_INT_PIN);

void setup() {
    /* setup pins */
    pinMode(LORA_LED_PIN, OUTPUT);
    pinMode(RFM95_RST_PIN, OUTPUT);
    pinMode(GREEN_CONT_LED_PIN, OUTPUT);
    pinMode(RED_CONT_LED_PIN, OUTPUT);
    pinMode(RELAY_PIN, OUTPUT);
    // no need to setup ADC_PIN, that is handled by analogRead()

    digitalWrite(RELAY_PIN, LOW); // THE MOST IMPORTANT PIN
    digitalWrite(RFM95_RST_PIN, HIGH);
    digitalWrite(GREEN_CONT_LED_PIN, HIGH); // start with yellow
    digitalWrite(RED_CONT_LED_PIN, HIGH);

    Serial.begin(9600); // baud rate 9600
    delay(100);

    Serial.println("Arduino LoRa RX Test!");

    /* manual reset */
    digitalWrite(RFM95_RST_PIN, LOW);
    delay(10);
    digitalWrite(RFM95_RST_PIN, HIGH);
    delay(10);

    /* initialise lora */
    while (!lora.init()) {
        Serial.println("LoRa radio init failed");
        while (1);
    }
    Serial.println("LoRa radio init OK!");

    /* Defaults after init are 433.0MHz, modulation GFSK_Rb250Fd250, +13dbM */
    if (!lora.setFrequency(RF95_FREQ)) {
        Serial.println("setFrequency failed");
        while (1);
    }
    Serial.print("Set Freq to: "); Serial.println(RF95_FREQ);
    lora.setPayloadCRC(false);

    // The default transmitter power is 13dBm, using PA_BOOST.
    // If you are using RFM95/96/97/98 modules which uses the PA_BOOST transmitter pin, then 
    // you can set transmitter powers from 5 to 23 dBm:
    lora.setTxPower(20, false);

    // 433.0MHz, 20dBm, Bw = 125 kHz, Cr = 4/5, Sf = 128chips/symbol, CRC off
}

uint8_t ledToggle = LOW;
uint32_t ledLastOn = 0;
uint16_t adcValue = 0;
uint8_t continuity = 0;
uint32_t lastADC = 0;
uint8_t printADC = 0;

void loop() {
    /* collect continuity info four times a second */
    if (millis() - lastADC > 250) {
        adcValue = analogRead(ADC_PIN);
        printADC++;
        if (printADC == 4) {
            Serial.print("ADC: ");
            Serial.println(adcValue);
            printADC = 0;
        }
        if (adcValue > ADC_THRESH) {
            digitalWrite(GREEN_CONT_LED_PIN, HIGH);
            digitalWrite(RED_CONT_LED_PIN, LOW);
            continuity = 1;
        } else {
            digitalWrite(GREEN_CONT_LED_PIN, LOW);
            digitalWrite(RED_CONT_LED_PIN, HIGH);
            continuity = 0;
        }
        lastADC = millis();
    }
    /* turn off lora LED */
    if (millis() - ledLastOn > 500) {
        digitalWrite(LORA_LED_PIN, LOW);
    }
    if (lora.available()) {
        /* Should be a message for us now */
        uint8_t buf[RH_RF95_MAX_MESSAGE_LEN];
        uint8_t len = sizeof(buf);

        if (lora.recv(buf, &len)) {
            Serial.print("Received: \"");
            Serial.print((char*) buf);
            Serial.print("\"\r\n");
            Serial.print("RSSI: ");
            Serial.println(lora.lastRssi(), DEC);
            if (len == 5 && strcmp(buf, "cork") == 0) {
                /* turn on lora LED */
                ledLastOn = millis();
                digitalWrite(LORA_LED_PIN, HIGH);
                
                /* Send a reply */
                if (continuity) {
                    uint8_t message[] = {'s', 't', 'o', 'p', '\0'};
                    lora.send(message, sizeof(message));
                    lora.waitPacketSent();
                    Serial.println("Sent reply \"stop\"\r\n");
                } else {
                    uint8_t message[] = {'s', 't', 'a', 'l', '\0'};
                    lora.send(message, sizeof(message));
                    lora.waitPacketSent();
                    Serial.println("Sent reply \"stal\"\r\n");
                }
            } else if (len == 7 && strcmp(buf, "IGNITE") == 0) {
                /* IGNITE */
                if (continuity) {
                    /* done */
                    digitalWrite(RELAY_PIN, HIGH);
                    delay(50); // relay pin triggers for 50ms
                    digitalWrite(RELAY_PIN, LOW);
                    uint8_t message[] = {'d', 'o', 'n', 'e', '\0'};
                    lora.send(message, sizeof(message));
                    lora.waitPacketSent();
                    Serial.println("Sent reply \"done\"\r\n");
                } else {
                    /* can't */
                    uint8_t message[] = {'c', 'a', 'n', 't', '\0'};
                    lora.send(message, sizeof(message));
                    lora.waitPacketSent();
                    Serial.println("Sent reply \"cant\"\r\n");
                }
            }
        } else {
            Serial.println("Receive failed");
        }
    }
}

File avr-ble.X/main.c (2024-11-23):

/*
radio datasheets:
https://cdn-learn.adafruit.com/downloads/pdf/adafruit-rfm69hcw-and-rfm96-rfm95-rfm98-lora-packet-padio-breakouts.pdf
https://cdn-shop.adafruit.com/product-files/3076/sx1231.pdf

avr-ble:
https://ww1.microchip.com/downloads/aemDocuments/documents/MCU08/ProductDocuments/UserGuides/AVR-BLE-Hardware-User-Guide-DS50002956B.pdf
*/

#define F_CPU 3333333

#include <avr/io.h>
#include <util/delay.h>
#include <avr/interrupt.h>
#include <avr/wdt.h>

#include <string.h>
#include <stdio.h>

#include "uart.h"
#include "tca.h"
#include "lora.h"

/* ARM_BUTTON_PIN - PC1 */
#define ARM_BUTTON_PIN        PIN1_bm
/* IGNITE_BUTTON_PIN - PD6 */
#define IGNITE_BUTTON_PIN     PIN6_bm
/* DC_BUZZER_PIN - PD1 */
#define DC_BUZZER_PIN         PIN1_bm

/* LORA_LED_PIN - PC0 */
#define LORA_LED_PIN          PIN0_bm
/* continuity LED green channel pin - PD5 */
#define GREEN_CONT_LED_PIN    PIN5_bm
/* continuity LED red channel pin - PD7 */
#define RED_CONT_LED_PIN      PIN7_bm
/* ignite status LED green channel pin - PA0 */
#define GREEN_IGN_LED_PIN     PIN0_bm
/* ignite status LED red channel pin - PF3 */
#define RED_IGN_LED_PIN       PIN3_bm

uint8_t ledToggle = 0;
uint32_t millis = 0;
uint32_t ledMillis = 0;
uint8_t receivedGood = 0;
uint8_t hasConnection = 0;
uint8_t mustRelease = 0;

void parse_lora(uint8_t * buf, uint8_t len, uint8_t status);
void sendIgnite(); // send ignite key to receiver
uint32_t armButtonDown; // how many milliseconds the arm button has been down for
uint8_t armButtonBuffer = 0;
uint8_t igniteButtonBuffer = 0;
uint8_t firstTick = 0;

int main() {
    /* pin init */
    PORTC.DIR |= LORA_LED_PIN;
    PORTD.DIR |= GREEN_CONT_LED_PIN;
    PORTD.DIR |= RED_CONT_LED_PIN;
    PORTA.DIR |= GREEN_IGN_LED_PIN;
    PORTF.DIR |= RED_IGN_LED_PIN;
    PORTD.DIR |= DC_BUZZER_PIN;
    PORTC.DIR &= ~ARM_BUTTON_PIN;
    PORTC.PIN1CTRL |= PORT_PULLUPEN_bm;
    PORTD.DIR &= ~IGNITE_BUTTON_PIN;
    PORTD.PIN6CTRL |= PORT_PULLUPEN_bm;
    
    PORTD.OUT |= GREEN_CONT_LED_PIN; // start yellow
    PORTD.OUT |= RED_CONT_LED_PIN;
    PORTA.OUT &= ~GREEN_IGN_LED_PIN; // start off
    PORTF.OUT &= ~RED_IGN_LED_PIN;
    uart_init(9600);
    if (tca_init()) {
        uart_tx("RTC could not initialise\r\n");
        while (1);
    }
    uart_tx("RTC successfully initialised\r\n");
    if(lora_init()) {
        uart_tx("lora could not initialise\r\n");
		while(1); // If init returns 0, error occur. Check connections and try again.
	}
    uart_tx("lora successfully initialised\r\n\r\n");
    register_lora_rx_event_callback(parse_lora);
    sei();
	while(1) {
		lora_receive();
        if ((PORTC.IN & ARM_BUTTON_PIN) == 0) {
            armButtonBuffer = 10;
        }
        if (armButtonBuffer) {
            armButtonDown++;
        }
        if (armButtonBuffer > 0) {
            armButtonBuffer--;
        } else {
            armButtonDown = 0;
        }
        if ((PORTD.IN & IGNITE_BUTTON_PIN) == 0) {
            igniteButtonBuffer = 10;
        }
        if (igniteButtonBuffer > 0) {
            igniteButtonBuffer--;
        }
        if (millis - ledMillis > 500 && receivedGood) {
            PORTC.OUT |= LORA_LED_PIN;
        }
        if (armButtonBuffer) {
            firstTick = 1;
            if (mustRelease == 0 && armButtonDown == 1) {
                /* turn off IGNITE LED */
                PORTA.OUT &= ~GREEN_IGN_LED_PIN;
                PORTF.OUT &= ~RED_IGN_LED_PIN;
            }
            if (hasConnection) {
                if (mustRelease == 0) {
                    PORTD.OUT |= DC_BUZZER_PIN;
                }
                if (armButtonDown == 1000) {
                    /* turn IGNITE LED to YELLOW */
                    PORTA.OUT |= GREEN_IGN_LED_PIN;
                    PORTF.OUT |= RED_IGN_LED_PIN;
                }
                if (igniteButtonBuffer && mustRelease == 0 && armButtonDown > 1000) {
                    /* turn IGNITE LED to YELLOW */
                    PORTA.OUT |= GREEN_IGN_LED_PIN;
                    PORTF.OUT |= RED_IGN_LED_PIN;
                    sendIgnite();
                    mustRelease = 1;
                    PORTD.OUT &= ~DC_BUZZER_PIN;
                } else if (igniteButtonBuffer && mustRelease == 0) {
                    mustRelease = 1;
                }
            }
        } else {
            if (firstTick) {
                PORTD.OUT &= ~DC_BUZZER_PIN;
                if (mustRelease == 0) {
                    /* turn off IGNITE LED */
                    PORTA.OUT &= ~GREEN_IGN_LED_PIN;
                    PORTF.OUT &= ~RED_IGN_LED_PIN;
                }
                if (igniteButtonBuffer == 0) {
                    mustRelease = 0;
                }
                firstTick = 0;
            }
        }
        _delay_ms(1);
        millis++;
	}
}

void parse_lora(uint8_t *buf, uint8_t len, uint8_t status) {
	//If error, return.
	if( status == IRQ_PAYLOAD_CRC_ERROR_MASK ) {
		// ...process error
		return;
	}
	uart_tx("Received: \"");
    uart_tx((const char *) buf);
    uart_tx("\"\r\n");
    uart_tx("RSSI: ");
    uint16_t rssi = lora_last_packet_rssi(433);
    char rssiStr[10];
    sprintf(rssiStr, "%d", rssi);
    uart_tx(rssiStr);
    uart_tx("\r\n\r\n");
    if (strcmp((const char *) buf, "stop") == 0) {
        /* received continuity OK */
        PORTD.OUT |= GREEN_CONT_LED_PIN;
        PORTD.OUT &= ~RED_CONT_LED_PIN;
        receivedGood = 1;
        hasConnection = 1;
    }
    if (strcmp((const char *) buf, "stal") == 0) {
        /* received continuity ERROR (no continuity) */
        PORTD.OUT &= ~GREEN_CONT_LED_PIN;
        PORTD.OUT |= RED_CONT_LED_PIN;
        receivedGood = 1;
        hasConnection = 1;
    }
    if (strcmp((const char *) buf, "done") == 0) {
        /* received ignite OK */
        PORTA.OUT |= GREEN_IGN_LED_PIN;
        PORTF.OUT &= ~RED_IGN_LED_PIN;
    }
    if (strcmp((const char *) buf, "cant") == 0) {
        /* received ignite ERROR */
        PORTA.OUT &= ~GREEN_IGN_LED_PIN;
        PORTF.OUT |= RED_IGN_LED_PIN;
    }
}

void sendIgnite() {
    uint8_t message[] = {0xFF, 0xFF, 0xFF, 0xFF, 'I', 'G', 'N', 'I', 'T', 'E', '\0'};
    lora_send(message, sizeof(message));
    uart_tx("Sent \"IGNITE\"\r\n");
}

/* TCA ISR - every second */
ISR(TCA0_OVF_vect) {
    uint8_t message[] = {0xFF, 0xFF, 0xFF, 0xFF, 'c', 'o', 'r', 'k', '\0'};
    lora_send(message, sizeof(message));
    uart_tx("Sent \"cork\"\r\n");
    if (receivedGood == 0) {
        /* didn't receive it last time - toggle continuity LED yellow */
        PORTD.OUT |= GREEN_CONT_LED_PIN;
        PORTD.OUT |= RED_CONT_LED_PIN;
        hasConnection = 0;
    }
    receivedGood = 0;
    PORTC.OUT &= ~LORA_LED_PIN;
    ledMillis = millis;
    /* The interrupt flag has to be cleared manually */
    TCA0.SINGLE.INTFLAGS &= TCA_SINGLE_OVF_bm;
}

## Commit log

2024-10-18 start of a plan & start of controller CAD
    [TalentcellPower.SLDPRT]
2024-11-17 control lora loop done, but test failed
    [main.c]
2024-11-17 interrupts are firing, but the data is not recognised
2024-11-17 removed serial startup requirement from itsy bitsy
    [Control.SLDASM, ControlCase.SLDPRT]
2024-11-17 LEDs in sync
2024-11-17 removed funny spi
2024-11-18 continuity light and button pins picked
2024-11-18 relay logic
2024-11-22 updated control box structure
    [Control.SLDASM, ControlCase.SLDPRT, TalentcellPower.SLDPRT]
2024-11-23 control box CAD done
    [Control.SLDASM, ControlCase.SLDPRT, ControlLid.SLDPRT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]
2024-11-23 cad changes and code changes
    [Control.SLDASM, ControlCase.STEP, ControlLid.STEP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]
2024-11-24 assembly fixed
    [Control.SLDASM, ControlTopShelf.SLDPRT]
2024-11-26 changed lora interrupt pin on itsy bitsy
2024-11-27 decreased switch time to 50ms
    [Control.SLDASM, ControlCase.SLDPRT, ControlCase.STEP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]
2024-11-29 CAD changes
    [Control.SLDASM, ControlCase.SLDPRT, ControlCase.STEP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]
2024-11-29 current sensıri
    [Corkstop.dxf, CurrentSensor.SLDPRT, CurrentSensor.STEP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]
2024-12-01 db power 23
2024-12-05 manual merge
    [ControlTopShelf.SLDPRT, ControlTopShelf.STEP]
2024-12-05 added control box CAD to readme
2024-12-05 fixed wonky cad
    [ControlCase.SLDPRT]
